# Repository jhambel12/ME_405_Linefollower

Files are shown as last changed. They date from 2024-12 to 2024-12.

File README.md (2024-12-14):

# ME_405_Linefollower

**Cal Poly Mechatronics Line Follower Robot**

This project involves a Romi robot configured and programmed using micropython to autonomously complete a line-following course and return to its initial start point. This involves line detection, bump detection, and relative position tracking. This work was completed by **Jack Ellis** and **Jacob Hambel**, with guidance and support from **Charlie Refvem**. 

---

## Main Features

- **Line Following Capability**: The robot uses infrared sensors to detect and follow a predefined line.
- **Obstacle Detection and Avoidance**: Equipped with bump sensors to handle unexpected obstacles.
- **Position Tracking**: Returns from the start box after completing the course.

---

## Components Used

### Hardware:
- **Romi Chassis and Components**
- **BNO055 IMU sensor**: Detects acceleration, angular rate, and magnetic fields. Note - handle with care as it is sensitive to impact.
- **Infrared Line Sensors**: Five ITR20001/T infrared sensors for line detection.
- **Bump Sensor**: Detects obstacles to avoid collisions.

### Mechanical Design Files:
- `Line Sensor Mount` - [View Line Sensor Mount](./CAD/Lower_Bracket.STL)  
- `Bump Sensor Mount` - [View Bump Sensor Mount](./CAD/Upper_Bracket.STL)  
- `Bump Sensor Bumper` - [Bump Sensor Bumper](./CAD/Bump_Sensor.STL)  
-    Bump sensor bumper is optional, the reason for its use in this project is to reduce the weight offset in the front.

---

## Wiring Information
- **Nucleo Pinout diagrams**
    See the Morpho Headers section on the [ST Nucleo-L475RG webpage](https://os.mbed.com/platforms/ST-Nucleo-L476RG/).  
- **Wiring Diagram**
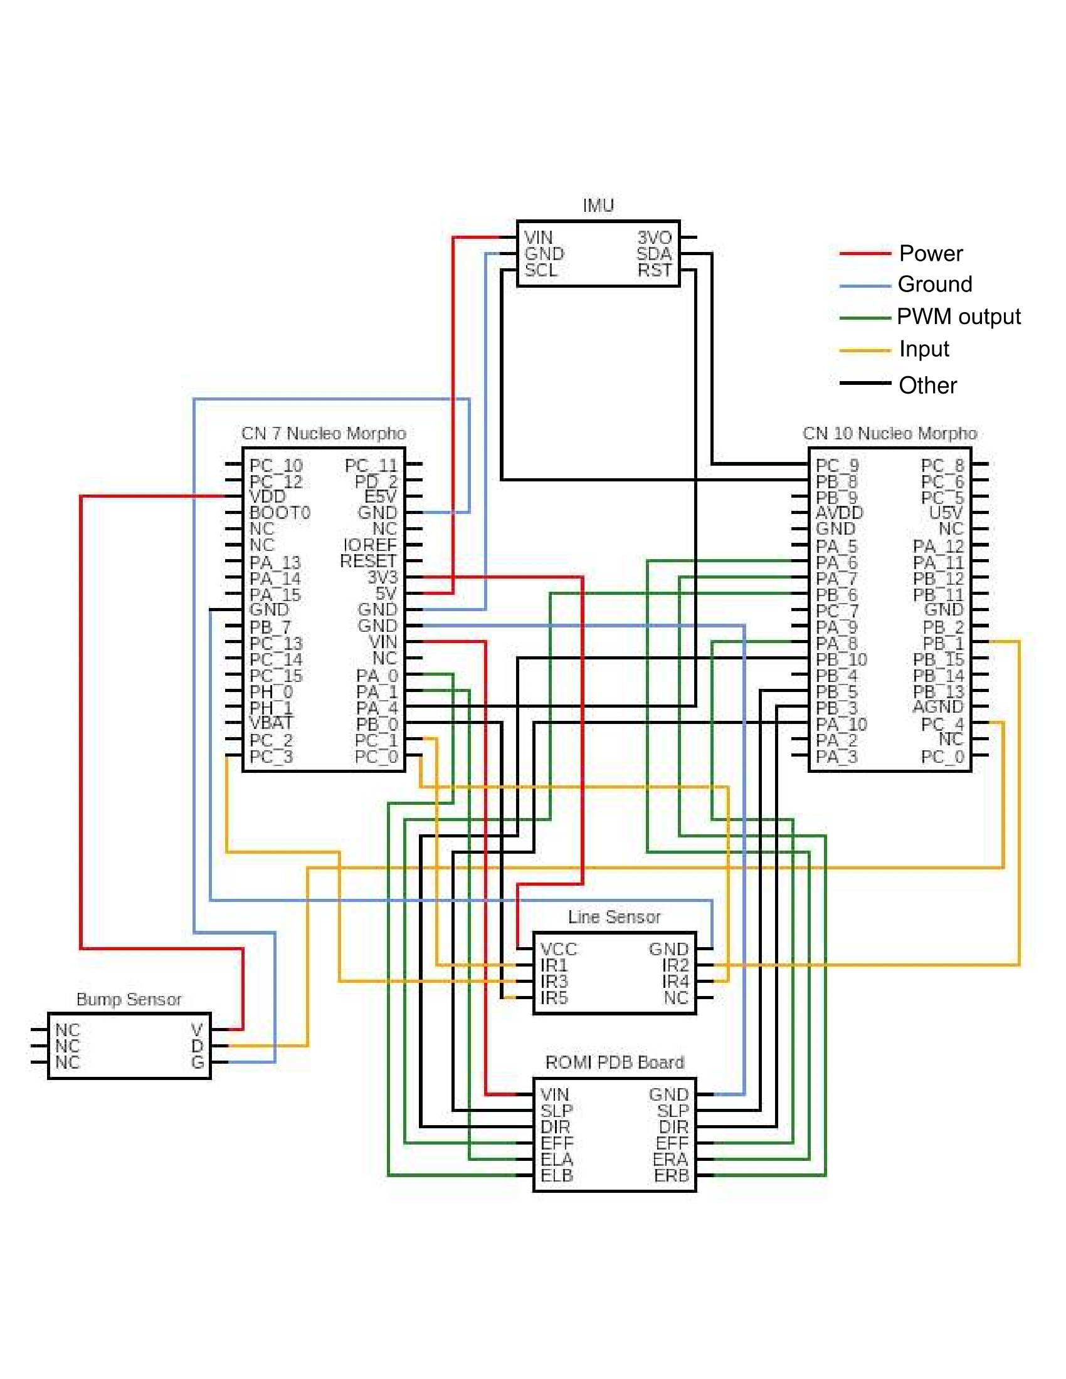
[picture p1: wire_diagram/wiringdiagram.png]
Wiring Diagram
  

- **Pin assignment table**    

| Pin Name Nucleo | Pin Mode | Connection | Pin Name on device |
| --- | --- | --- | --- |
| PB_5 | Output, Push/Pull | Left Motor Enable | Not Sleep text |
| PB_3 | Output, Push/Pull | Left Motor Direction | DIR |
| PA_8 | Timer 1 CH 1 | Left Motor effort | PWM |
| PA_10 | Output, Push/Pull | Right Motor Enable | Not Sleep text | 
| PB_10 | Output, Push/Pull | Right Motor Direction | DIR |
| PB_6 | Timer 4 CH 1 | Right Motor effort | PWM |
| PA_6 | Timer 3 CH 1 | Right Encoder | ERB |
| PA_7 | Timer 3 CH 2 | Right Encoder | ERA |
| PA_0 | Timer 2 Ch 1 | Left Encoder | ELB |
| PA_1 | Timer 2 Ch 2 | Left Encoder | ELA |
| PC_1 | Analog input | Line sensor | IR1 |
| PB_1 | Analog input | Line sensor | IR2 |
| PC_3 | Analog input | Line sensor | IR3 |
| PC_0 | Analog input | Line sensor | IR4 |
| PB_0 | Analog input | Line sensor | IR5 |
| PC_4 | Analog input | Bump sensor | D |
| PA_4 | Output, Push/Pull | Reset Pin for IMU | RST |
| PB_8 | I2C1 SCL | I2C1 clock for I2C bus | SCL |
| PB_9 | I2C1 SDA | I2C1 serial data for I2C bus | SDA |

---

## Software

The control system implements a **PI control loop**, using encoder data and line sensor readings as feedback to maintain line tracking and accurate trajectory. This program uses cooperative multitasking in a finite state machine to ensure all tasks run on time. To accomplish this, the scheduler is used with priority and duration

### Python Files:
- **`main.py`**: Main program orchestrating the robot’s behavior.  
[View main File](./code/main.py)  
- **`motor.py`**: Controls motor operations.  
[View Motor File](./code/motor.py)  
- **`encoder.py`**: Handles data from the encoders.  
[View IMU File](./code/encoder.py)  
- **`BNO055.py`**: Interface for the BNO055 sensor (if used).  
[View Line Sensor File](./code/BNO055.py)  
- **`irsensor.py`**: Reads data from the infrared sensors.  
[View Bump Sensor File](./code/irsensor.py)  
- **`bumpsensor.py`**: Reads data from the bump sensor.  
[View cotask File](./code/bumpsensor.py)  
- **`cotask.py`**: Manages cooperative multitasking.  
[View task_share File](./code/cotask.py)  
- **`task_share.py`**: Facilitates shared data between tasks.  
[View Main File](./code/task_share.py)  

### Code Functionality:
Main holds the task structure and is the file that runs when the robot is in motion. The code operates as a finite state machine, and it has five tasks. The following task diagram shows the tasks and the shared variables between them. 
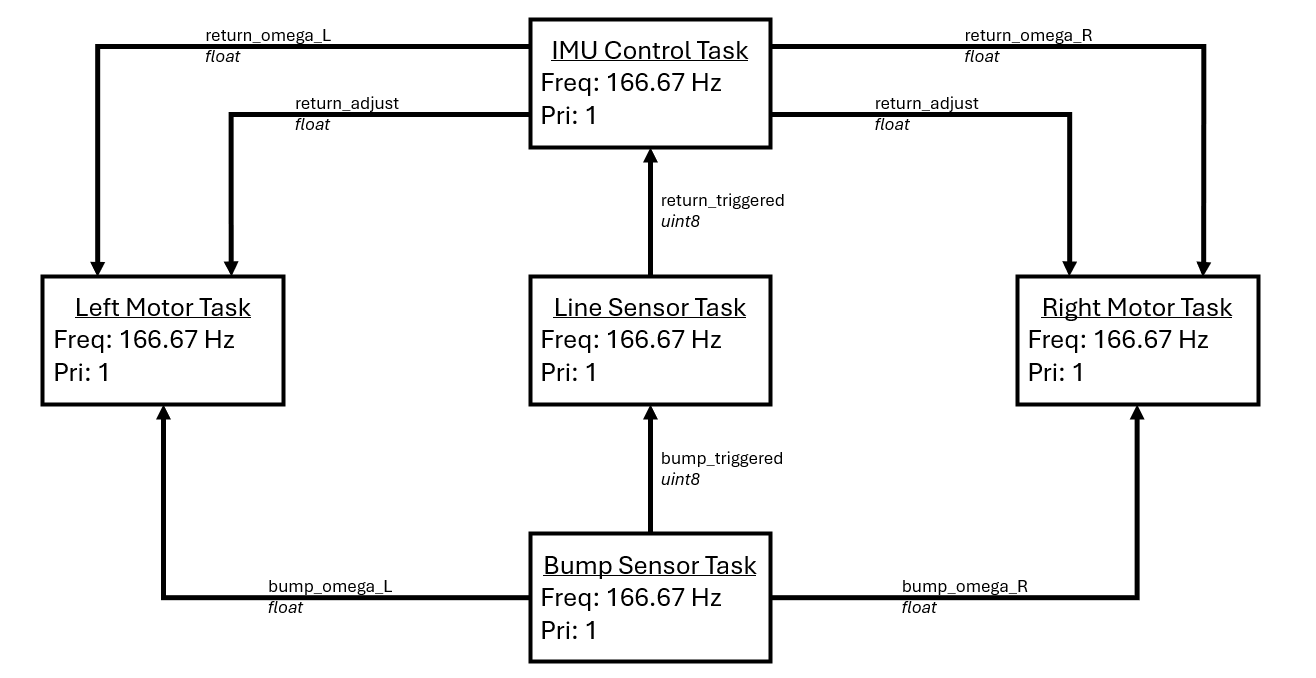
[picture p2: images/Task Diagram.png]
Task Diagram
 

Below, state transition diagrams are provided for each of the tasks.
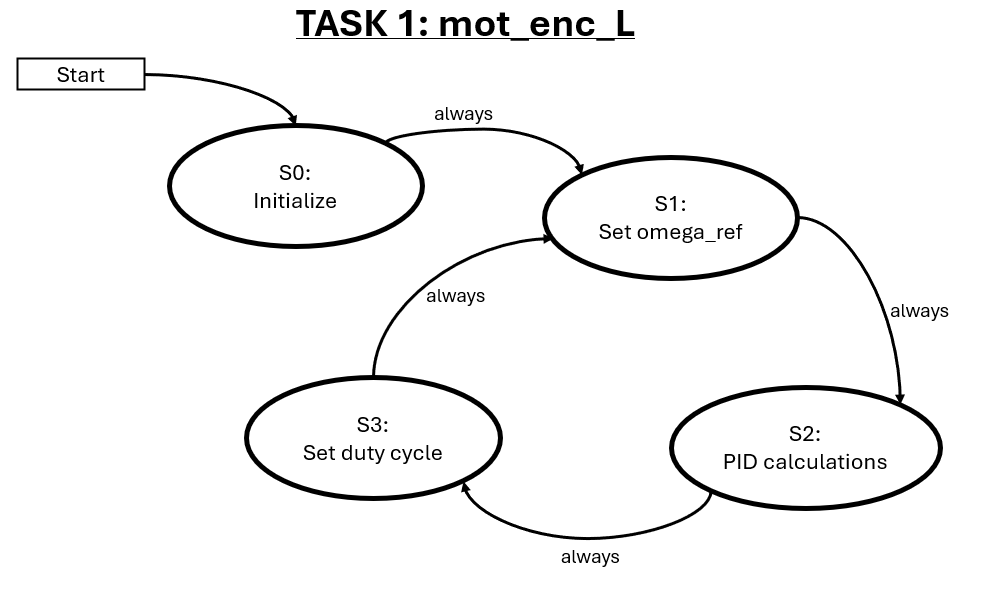
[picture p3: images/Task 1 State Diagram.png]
Task 1
 
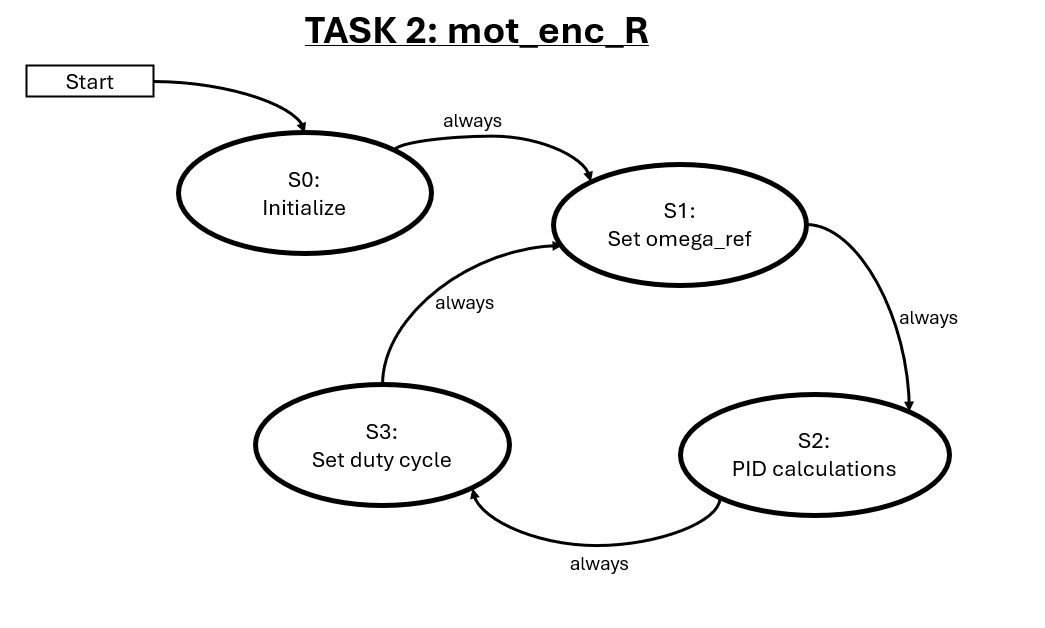
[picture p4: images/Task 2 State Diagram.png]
Task 2
 
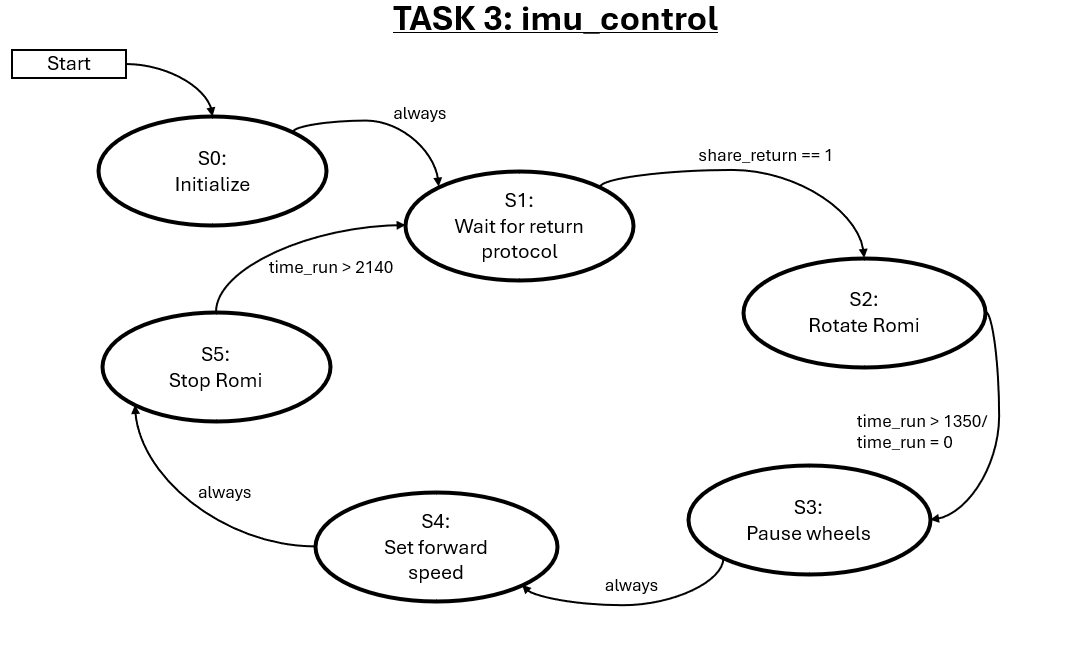
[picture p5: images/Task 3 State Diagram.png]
Task 3
 
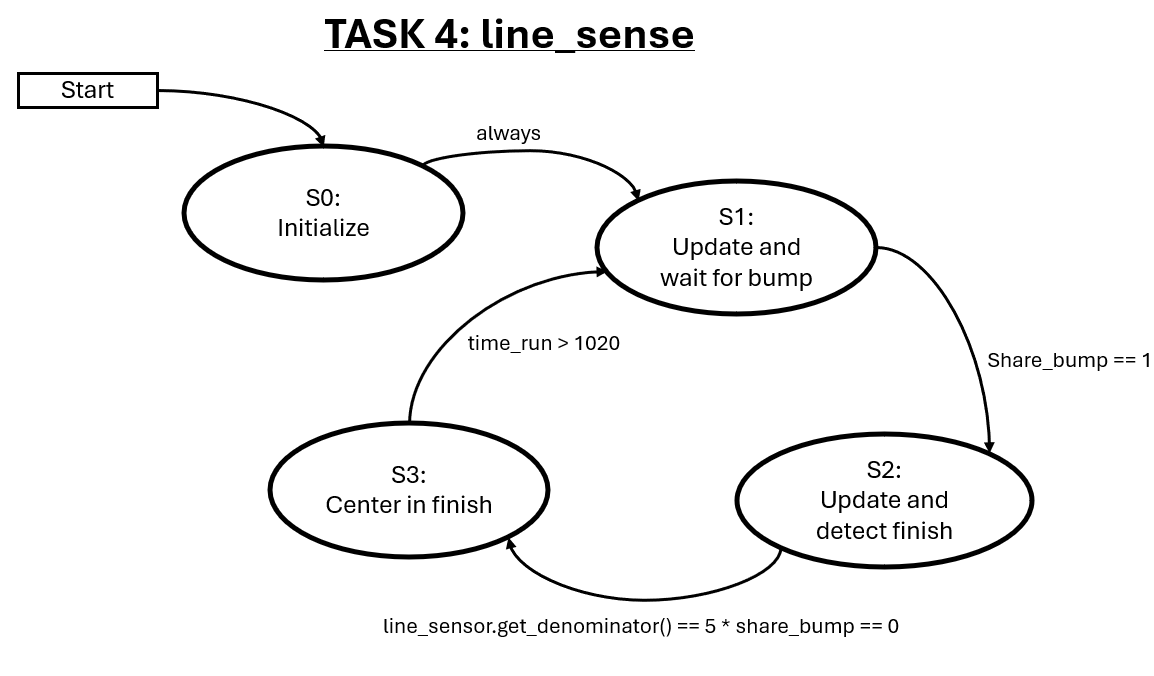
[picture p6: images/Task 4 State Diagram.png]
Task 4
 
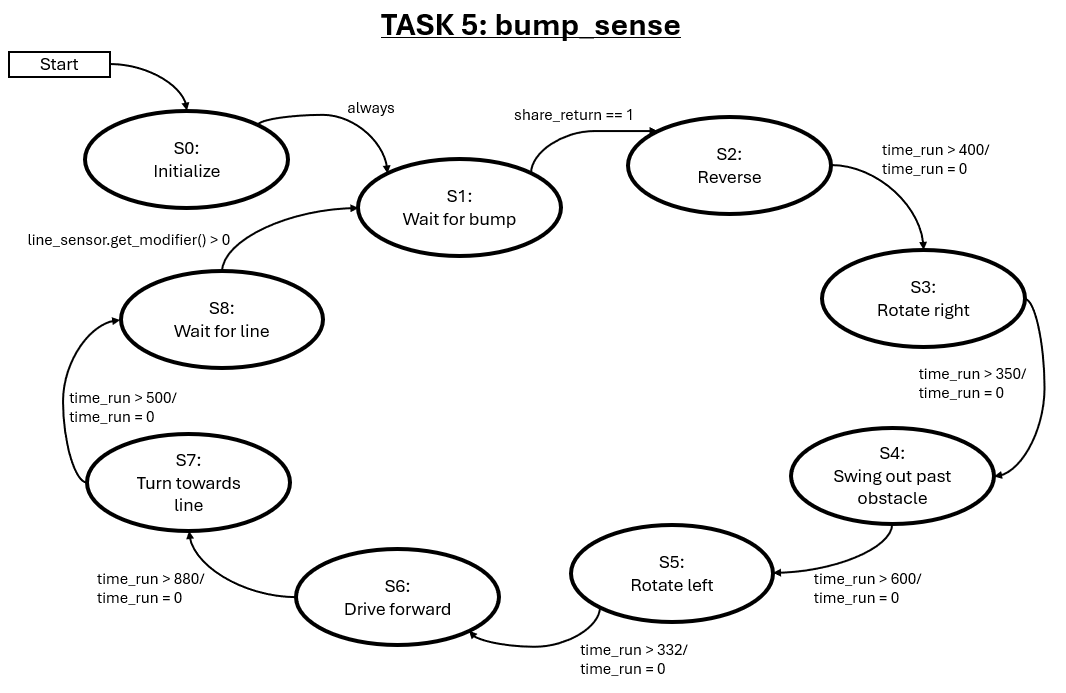
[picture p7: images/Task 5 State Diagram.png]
Task 5
 

Within these tasks, classes are referenced to handle particular functions of the sensors, motor controller, and the IMU that the code interacts with. This keeps the length reasonable and improves the readibility of the code. Overall, the flow of the code wants to stay in line following mode. If the bump sensor is triggered, the obstacle avoidance measures will be taken until it finds a line again. After the bump sensor is triggered, the line sensor mode will look for all 5 sensors to detect a line. When this happens, that means Romi has found the end box. Romi will then proceed to the center of the box and rotate back to its original heading. After a brief pause, the Romi will begin driving straight on the original heading for a specified time until it returns into the start box. Then, it will stop in the start box completing the run of the course. Below, the functionality and usage of the imported files and classes is discussed.

#### Motor
The motor class is responsible for updating the effort, direction, and enabling the motors. This class is called in 2 tasks by main to control each motor. The effort of the motor is output from a PWM at a duty cycle specified by the controller to attempt to create zero steady state error between the encoder readings and the omega reference. 

#### Encoder
The encoder class has several methods, each of which serve as getting data from the encoder. One method, **`update`** updates the encoder position with the current position. The method **`get_delta`** reads the difference between the current and last encoder reading. **`get_position`** returns the current position. These functions, combined with the use of **'utime.ticks()`** allows for calculation of the actual wheel speed. 

#### Line Sensor
The irsensor class is responsible for gathering the analog readings of the 5 infrared sensors, screening them against a threshold value for black or white, and returning them as a true or false. This class compiles the readings of the sensors into a 5 value list. This is convenient because based on which sensor reads the black value of 1, that is where the line is. To use this as feedback, each position is assigned a value, -4,2,0,2,4 reading left to right. Performing a dot product on these lists determines a value, either positive or negative, that becomes a modifier on the wheel speed set points. The class then returns this modifier for use in the control loop.

#### IMU
The BNO055 class is responsible for gathering readings from the IMU. There are many features of this class that are unused. Mainly, data regarding the heading and yaw rate are used in conjunction with wheel speed data from the encoders to track the position relative to start. The data is sent over the I2C bus for the microcontroller and updated each time the class is called.

#### Bump Sensor
The bumpsensor class is used when the robot encounters the wall. The wall is an 8 inch by 8 inch square. The bump sensor becomes an active low when it has been triggered. This is used to transfer out of the line follower mode and into the obstacle avoidance mode.

#### Cotask
This file is provided for this project. Authored by Dr. Ridgely, **`cotask`** contains classes that can run cooperatively scheduled tasks in the context of a multitasking system. It uses the input scheduling algorithm to run tasks on time and in the proper order using closs called **`CoTaskList`**. 

#### Task_share
This file is provided for this project. Authored by Dr. Ridgely, **`task_share`** contains a class to allow tasks to share data without the risk of interrupts corrupting that data. This is very useful as variables may be shared between tasks without the need for global variables.
  
---

## Video
Line follower in action:  
Watch the Video (https://youtu.be/625d_27x-ZY)

---

## Photos
Romi Front View:  
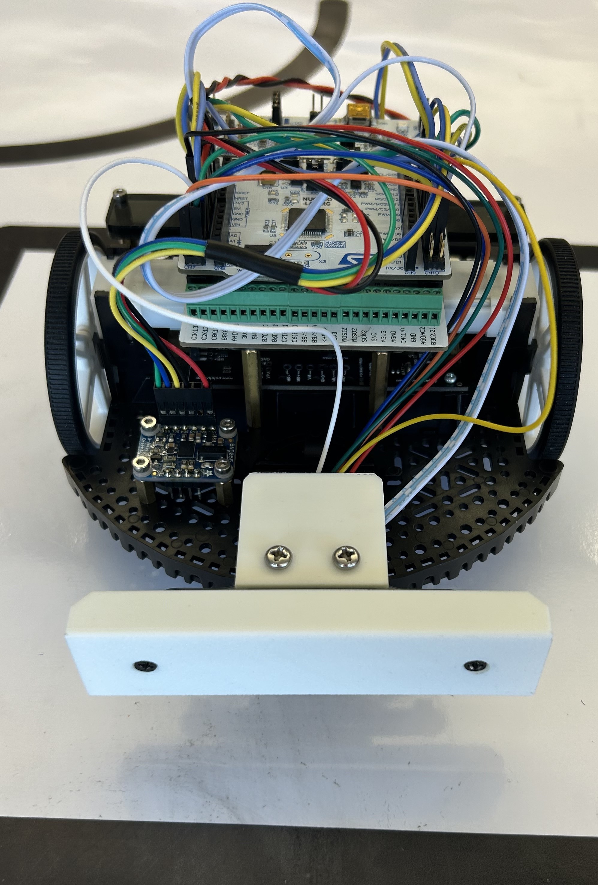
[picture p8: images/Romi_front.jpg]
Robot Front View
  
Romi Top View:  
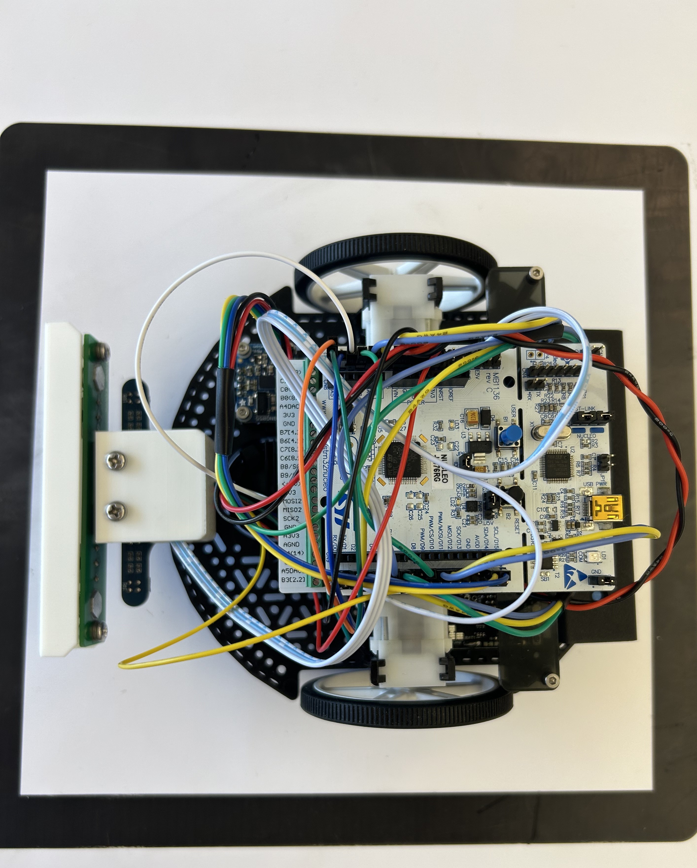
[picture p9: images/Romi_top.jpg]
Robot Top View
  
Romi Side View:  
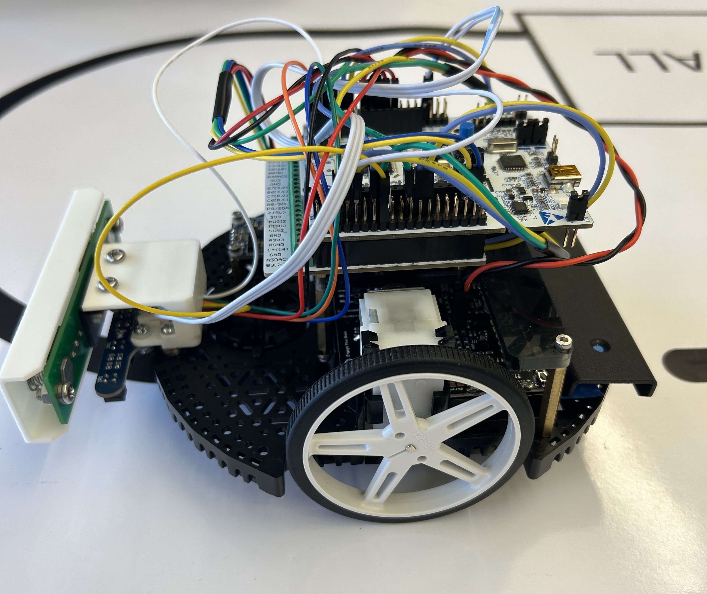
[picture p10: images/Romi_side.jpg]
Robot Side View
  
Romi Isometric View:  
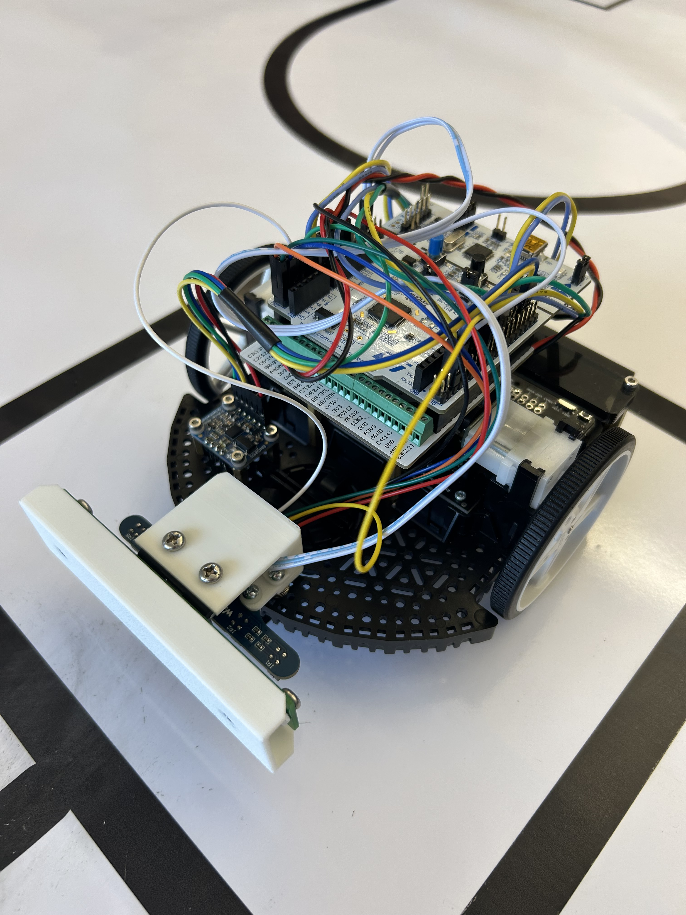
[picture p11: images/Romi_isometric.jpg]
Robot Isometric View
  
Sensor Mounting:  
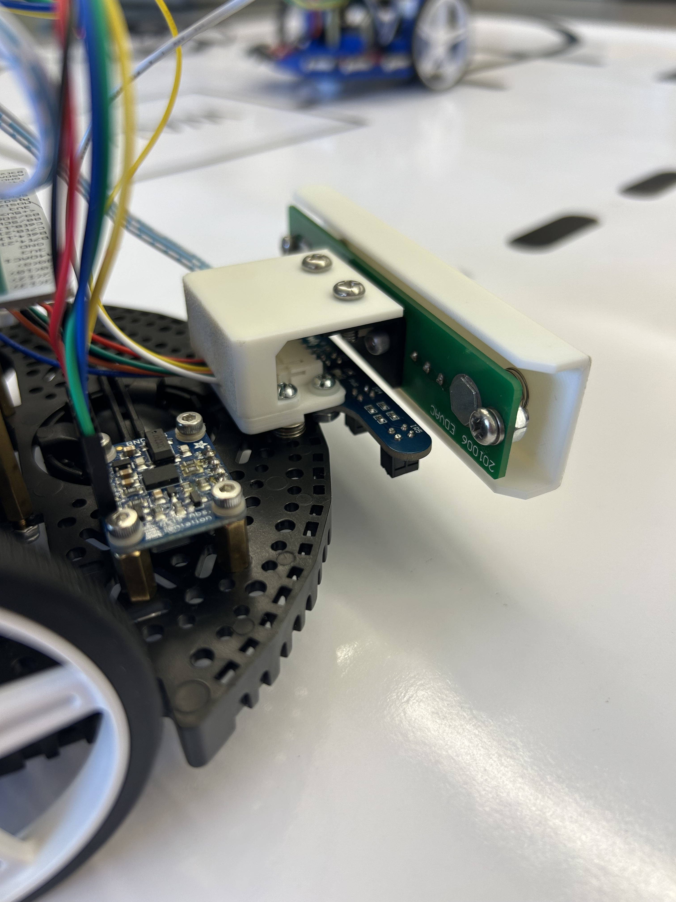
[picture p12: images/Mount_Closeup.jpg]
Sensor Mounting
  
Line Sensor Orientation:  
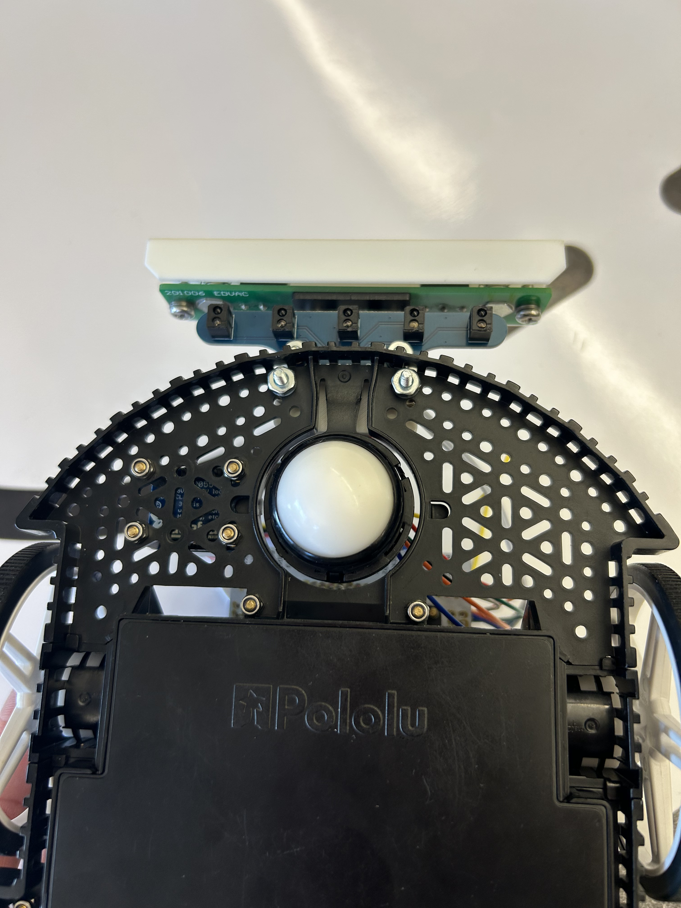
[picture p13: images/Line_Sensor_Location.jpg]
Line Sensor Orientation
  

---

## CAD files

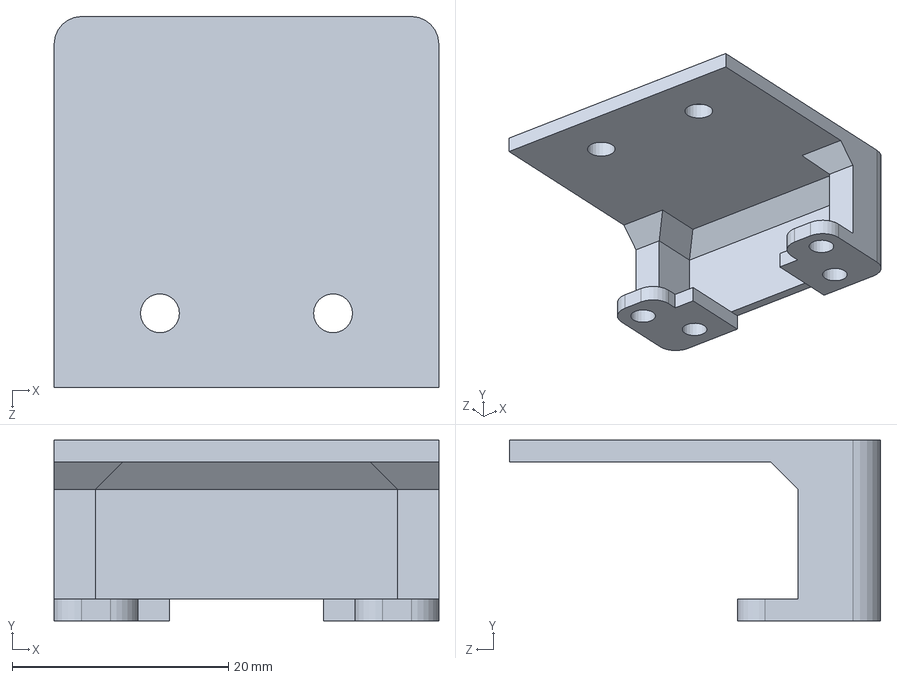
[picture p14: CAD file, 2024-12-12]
CAD/Upper_Bracket.SLDPRT
35.6 x 16.7 x 34.3 mm

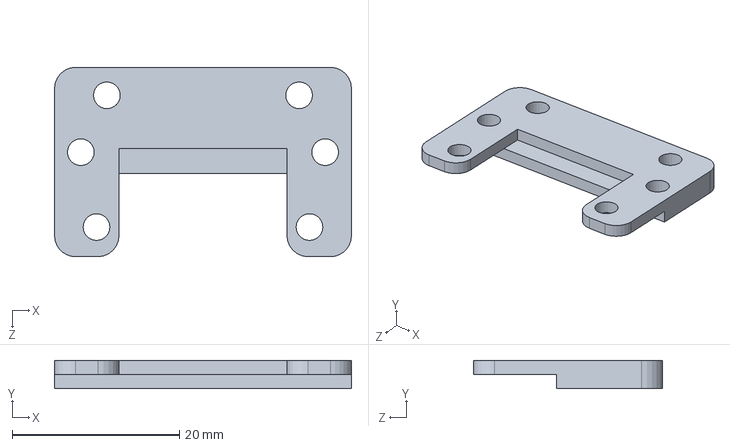
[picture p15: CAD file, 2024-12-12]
CAD/Lower_Bracket.SLDPRT
35.6 x 3.40 x 22.7 mm

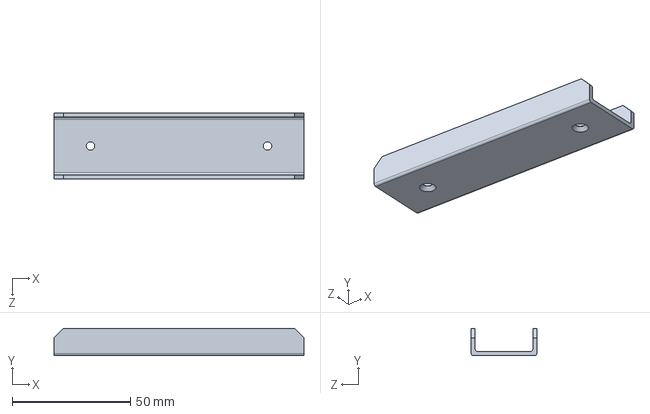
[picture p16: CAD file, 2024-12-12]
CAD/Bump_Sensor.SLDPRT
105.5 x 11.5 x 27.9 mm

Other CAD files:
CAD/Bump_Sensor.STL
CAD/Lower_Bracket.STL
CAD/Upper_Bracket.STL

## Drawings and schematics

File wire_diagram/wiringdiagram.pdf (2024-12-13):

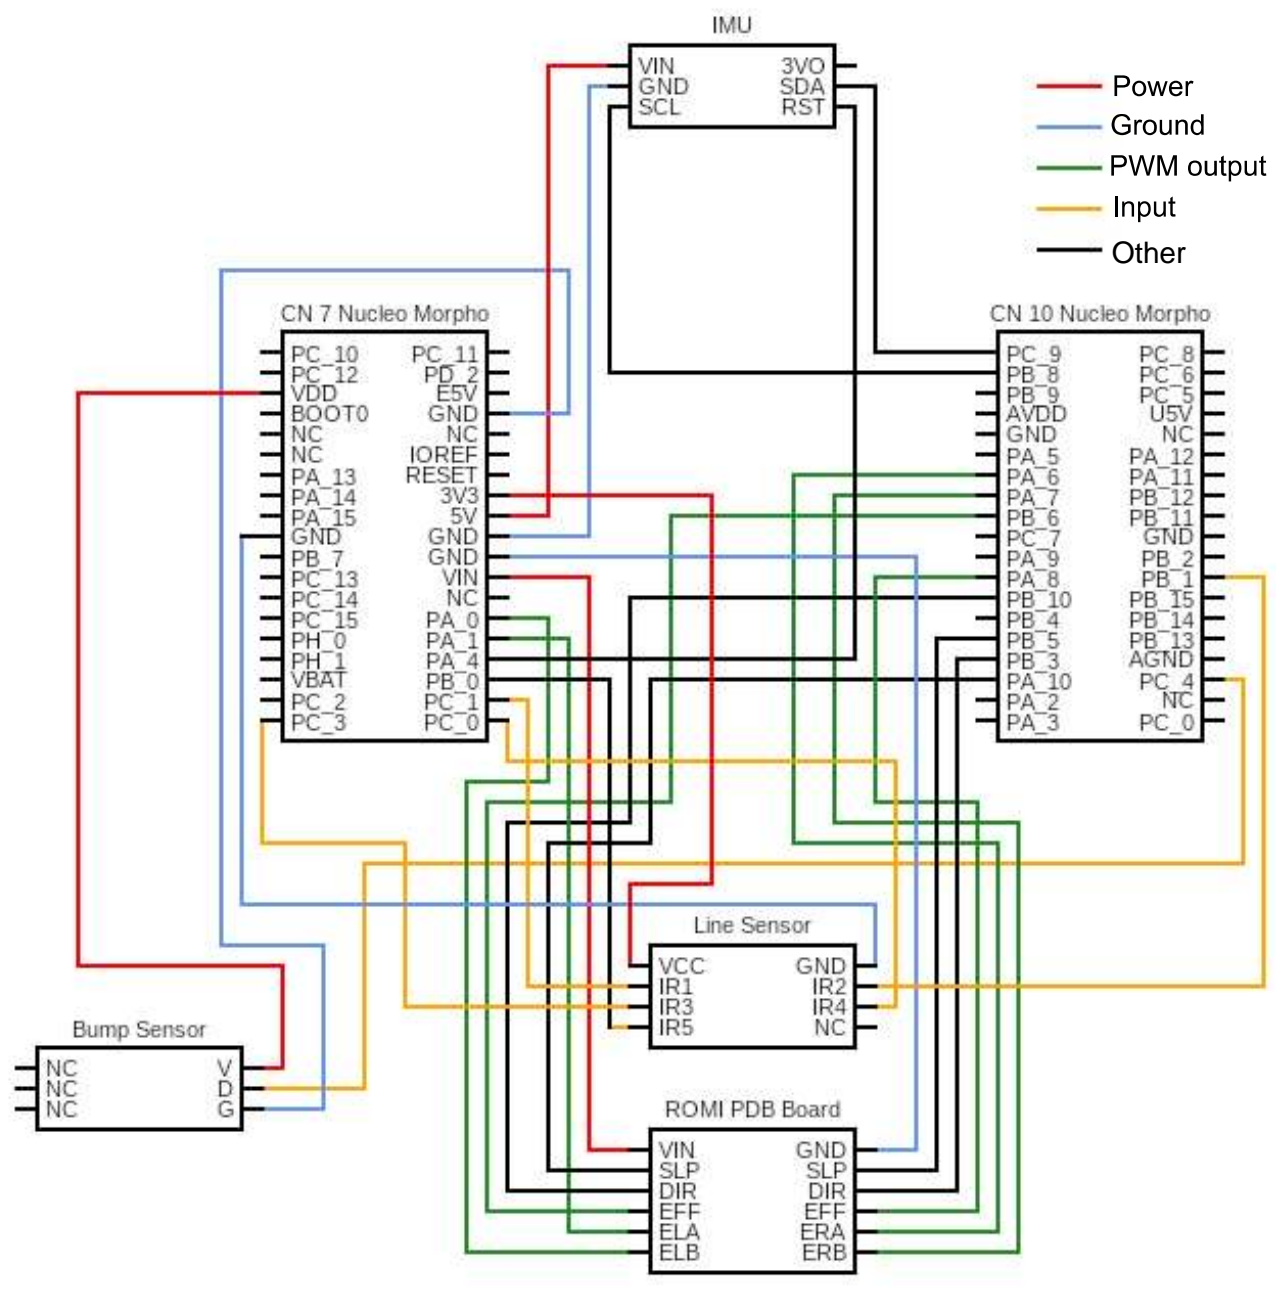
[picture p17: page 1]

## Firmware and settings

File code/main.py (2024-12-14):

'''
@file          main.py
@brief         Main script for autonomous course navigation of a Romi robot
@details       This script implements the control necessary for a Romi differential
               drive robot to navigate a course using line sensors and a bump
               sensor to determine the path for the Romi to take. Each motor 
               operates with a PID control loop using feedback from encoders and an
               IMU as needed.
@author        Jack Ellis, Jacob Hambel
@date          December 13, 2024
'''

#==================================================================================#
# Import necessary modules and classes                                             #
#==================================================================================#

import cotask
import task_share
import gc
import utime

from pyb import Pin, Timer, I2C
from array import array
from math import pi

from encoder import Encoder
from motor import Motor
from BNO055 import BNO055
from irsensor import IRSensor
from bumpsensor import Bumpsensor

#==================================================================================#
# Tasks                                                                            #
#==================================================================================#

# Task 1
def mot_enc_L(shares):
    '''
    @brief    Task 1: Control task for the left motor
    @details  This task intializes the left motor and encoder, performs the PID 
              control calculations, and sets the duty cycle.
    '''

    share_bump , share_omega_L , share_return , share_return_omega_L ,\
    share_heading_adjust = shares

    state = 0
    while True:
        
        # Initialize necessary variables and prepare the motor and encoder
        if state == 0:
            mot_L.enable()          # Enable the left motor
            enc_L.zero()            # Zero the encoder position
            old = utime.ticks_us()  # Store the current time
            mot_L.set_dir(True)     # Set motor direction
            K_p = 130               # Proportional gain constant
            K_i = 2                 # Integral gain constant
            K_d = 60               # Derivative gain constant
            err_old = 0             # Old error value for derivative control
            int_err = 0             # Integral error for integral control
            state = 1      

        # Detect if either the bump protocol or return protocol are active, and use
        # their prescribed velocities if they are. Otherwise, default to the line
        # sensor for control
        elif state == 1:
            if share_bump.get() == 1:
                int_err = 0
                omega_ref = share_omega_L.get()
            elif share_return.get() == 1:
                int_err = 0
                omega_ref = share_return_omega_L.get() + share_heading_adjust.get()
            else:
                adjust = line_sensor.get_modifier()
                omega_ref = (V_romi + ((adjust*V_romi)/4)) / r_wheel
            state = 2

        # Perform the encoder reading of velocity and calculation of errors for the
        # PID loop
        elif state == 2:
            now = utime.ticks_us()
            t_step = utime.ticks_diff(now, old)
            old = now
            enc_L.update()
            omega_meas = enc_L.get_delta() * ((12500 * pi) / 9) // t_step
            err = (omega_ref - omega_meas)
            int_err += err * t_step
            int_err = max(-20, min(int_err, 20))
            dif_err = (err - err_old) // t_step
            err_old = err
            state = 3

        # Calculate and set the duty cycle using the PID function
        elif state == 3:
            duty = (K_p * (omega_ref - abs(omega_meas)) + K_i * int_err
                    + K_d * dif_err)/28
            mot_L.set_duty(duty)
            state = 1

        yield None

#----------------------------------------------------------------------------------#

# Task 2
def mot_enc_R(shares):
    '''
    @brief    Task 2: Control task for the right motor
    @details  This task initializes the right motor and encoder, performs the PID
              control calculations, and sets the duty cycle.
    '''

    share_bump , share_omega_R , share_return , share_return_omega_R ,\
    share_heading_adjust = shares

    state = 0
    while True:
        
        # Initialize necessary variables and prepare the motor and encoder
        if state == 0:
            mot_R.enable()          # Enable the right motor
            enc_R.zero()            # Zero the encoder position
            old = utime.ticks_us()  # Store the current time
            mot_L.set_dir(True)     # Set motor direction
            K_p = 130               # Proportional gain constant
            K_i = 2                 # Integral gain constant
            K_d = 60               # Derivative gain constant
            err_old = 0             # Old error value for derivative control
            int_err = 0             # Integral error for integral control
            state = 1      

        # Detect if either the bump protocol or return protocol are active, and use
        # their prescribed velocities if they are. Otherwise, default to the line
        # sensor for control
        elif state == 1:
            if share_bump.get() == 1:
                int_err = 0
                omega_ref = share_omega_R.get()
            elif share_return.get() == 1:
                int_err = 0
                omega_ref = share_return_omega_R.get() - share_heading_adjust.get()
            else:
                adjust = line_sensor.get_modifier()
                omega_ref = (V_romi - ((adjust*V_romi)/4)) / r_wheel
            state = 2

        # Perform the encoder reading of velocity and calculation of errors for the
        # PID loop
        elif state == 2:
            now = utime.ticks_us()
            t_step = utime.ticks_diff(now, old)
            old = now
            enc_R.update()
            omega_meas = enc_R.get_delta() * ((12500 * pi) / 9) // t_step
            err = (omega_ref - omega_meas)
            int_err += err * t_step
            int_err = max(-20, min(int_err, 20))
            dif_err = (err - err_old) // t_step
            err_old = err
            state = 3

        # Calculate and set the duty cycle using the PID function
        elif state == 3:
            duty = (K_p * (omega_ref - abs(omega_meas)) + K_i * int_err
                    + K_d * dif_err)/23.34
            mot_R.set_duty(duty)
            state = 1

        yield None

#----------------------------------------------------------------------------------#

# Task 3
def imu_control(shares):
    '''
    @brief    Task 3: Control task for the IMU
    @details  This task saves the initial heading of the Romi to be used for the 
              return protocol. Once the return protocol is triggered, the IMU
              heading feedback controls the motors.
    '''

    share_return , share_return_omega_L , share_return_omega_R ,\
    share_heading_adjust = shares

    state = 0
    time_run = 0
    while True:

        # Take initial heading reading
        if state == 0:
            start_heading = imu.euler("head")
            state = 1

        # Detect of the return protocol needs to be executed
        elif state == 1:
            if share_return.get() == 1:
                share_return_omega_L.put(0)
                share_return_omega_R.put(0)
                old = utime.ticks_ms()
                state = 2
        
        # Rotate the Romi to generally face the starting box
        elif state == 2:
            now = utime.ticks_ms()
            time_run += utime.ticks_diff(now, old)
            old = utime.ticks_ms()
            mot_L.set_dir(False)
            return_omega_L.put(8)
            return_omega_R.put(8)
            if time_run > 1350:
                time_run = 0
                state = 3

        # Stop the Romi to ensure a smooth start to the return
        elif state == 3:
            mot_L.set_dir(True)
            return_omega_L.put(0)
            return_omega_R.put(0)
            state = 4

        # Set both wheels to a high speed to return quickly
        elif state == 4:
            return_omega_L.put(23)
            return_omega_R.put(23)
            old = utime.ticks_ms()
            state = 5

        # Use heading feeback to align the Romi and keep it on course to the start
        # box. After reaching the start box, disable the motors
        elif state == 5:
            now = utime.ticks_ms()
            time_run += utime.ticks_diff(now, old)
            old = utime.ticks_ms()
            current_heading = imu.euler("head")
            heading_error = current_heading - start_heading
            if heading_error > pi:
                share_heading_adjust.put(1)
            elif heading_error < pi:
                share_heading_adjust.put(-1)
            else:
                share_heading_adjust.put(0)
            if time_run > 2140:
                mot_L.disable()
                mot_R.disable()
                state = 1

        yield None

#----------------------------------------------------------------------------------#

# Task 4
def line_sense(shares):
    '''
    @brief    Task 4: Control task for the line sensors
    @details  This task updates the line sensor readings to prepare a new adjustment
              value for the motors to maintain orientation along the line. After
              cleairng the obstacle, the line sensor class prepares to detect the 
              trigger for the return protocol once entering the finish box.
    '''

    share_bump , share_return = shares

    state = 0
    time_run = 0
    while True:
        
        if state == 0:
            share_return.put(0)
            line_sensor.update()
            state = 1
        
        # Update the line sensor reading and detect if the obstacle has occured
        elif state  == 1:
            if share_bump.get() == 1:
                state = 2
            line_sensor.update()

        # Update the line sensor reading, and once the obstacle protocol has been
        # executed and the finish box is detected, begin the return protocol
        elif state == 2:
            line_sensor.update()
            if line_sensor.get_denominator() == 5 and share_bump.get() == 0:
                old = utime.ticks_ms()
                state = 3

        # Center in the finish box, and relinquish control to the IMU for the
        # return
        elif state == 3:
            now = utime.ticks_ms()
            time_run += utime.ticks_diff(now, old)
            old = utime.ticks_ms()
            if time_run > 1020:
                share_return.put(1)
                state = 1

        yield None

#----------------------------------------------------------------------------------#

# Task 5
def bump_sense(shares):
    '''
    @brief    Task 5: Control task for the bump sensor
    @details  The bump sensor contrl task monitors the bump sensor for triggering,
              and once triggered, it sends desired motor speeds to the motor 
              classes to navigate around the obstacle. Once clearing the obstacle
              and returning to the line, it reliquishes control to the line
              sensors.
    '''

    share_bump, share_omega_L, share_omega_R = shares

    state = 0
    time_run = 0
    while True:
        
        if state == 0:
            share_bump.put(0)
            state =1

        # Detect when a bump occurs and prepare the system to respond
        elif state == 1:
            if bump_sensor.detect() < 2000:
                share_bump.put(1)
                share_omega_L.put(0)
                share_omega_R.put(0)
                mot_L.set_dir(False)
                mot_R.set_dir(False)
                old = utime.ticks_ms()
                state = 2
        
        # Reverse from the obstacle
        elif state == 2:
            now = utime.ticks_ms()
            time_run += utime.ticks_diff(now, old)
            old = utime.ticks_ms()
            share_omega_L.put(8)
            share_omega_R.put(8)
            if time_run > 400:
                time_run = 0
                state = 3
        
        # Rotate right
        elif state == 3:
            now = utime.ticks_ms()
            time_run += utime.ticks_diff(now, old)
            old = utime.ticks_ms()
            mot_L.set_dir(True)
            share_omega_L.put(12)
            share_omega_R.put(12)
            if time_run > 350:
                time_run = 0
                state = 4

        # Drive forward to avoid the obstacle
        elif state == 4:
            now = utime.ticks_ms()
            time_run += utime.ticks_diff(now, old)
            old = utime.ticks_ms()
            mot_R.set_dir(True)
            share_omega_L.put(18)
            share_omega_R.put(18)
            if time_run > 600:
                time_run = 0
                state = 5

        # Rotate left
        elif state == 5:
            now = utime.ticks_ms()
            time_run += utime.ticks_diff(now, old)
            old = utime.ticks_ms()
            mot_L.set_dir(False)
            share_omega_L.put(12)
            share_omega_R.put(12)
            if time_run > 332:
                time_run = 0
                state = 6

        # Drive forward past the obstacle
        elif state == 6:
            now = utime.ticks_ms()
            time_run += utime.ticks_diff(now, old)
            old = utime.ticks_ms()
            mot_L.set_dir(True)
            share_omega_L.put(16)
            share_omega_R.put(16)
            if time_run > 880:
                time_run = 0
                state = 7

        # Turn back towards the path
        elif state == 7:
            now = utime.ticks_ms()
            time_run += utime.ticks_diff(now, old)
            old = utime.ticks_ms()
            share_omega_L.put(4)
            share_omega_R.put(18)
            if time_run > 500:
                time_run = 0
                state = 8

        # Continue straight until ready to relinquich control to the line sensors
        elif state == 8:
            now = utime.ticks_ms()
            time_run += utime.ticks_diff(now, old)
            old = utime.ticks_ms()
            share_omega_L.put(10)
            share_omega_R.put(10)
            if line_sensor.get_modifier() > 0:
                time_run = 0
                share_bump.put(0)
                state = 1

        yield None

#==================================================================================#
# Hardware Initialization and System Parameters                                    #
#==================================================================================#

# Motor objects
tim_L = Timer(1, freq=20_000)       # Timer for left motor
tim_R = Timer(4, freq=20_000)       # Timer for right motor
mot_L = Motor(tim_L, Pin.cpu.B5, Pin.cpu.B3, Pin.cpu.A8)    # Left motor object
mot_R = Motor(tim_R, Pin.cpu.A10, Pin.cpu.B10, Pin.cpu.B6)  # Right motor object

#----------------------------------------------------------------------------------#

# Encoder objects
enc_L = Encoder(2, 65535, 0, Pin.cpu.A0, Pin.cpu.A1)  # Left encoder object
enc_R = Encoder(3, 65535, 0, Pin.cpu.A6, Pin.cpu.A7)  # Right encoder object

#----------------------------------------------------------------------------------#

# Line sensor object
line_sensor = IRSensor([Pin(Pin.board.PC1), Pin(Pin.board.PB1), Pin(Pin.board.PC3), 
               Pin(Pin.board.PC0), Pin(Pin.board.PB0)])     # Line sensor object

#----------------------------------------------------------------------------------#

# Bump sensor object
bump_sensor = Bumpsensor(Pin(Pin.board.PC4))        # Bump sensor object

#----------------------------------------------------------------------------------#

# IMU setup
res_pin = Pin(Pin.cpu.A4, mode=Pin.OUT_PP)      # Reset pin for IMU
res_pin.low()
utime.sleep_ms(10)
res_pin.high()
utime.sleep_ms(650)
i2c = I2C(1, I2C.CONTROLLER, baudrate=400000)   # I2C bus for IMU
imu = BNO055(i2c)                               # IMU object
utime.sleep_ms(100)
imu.op_mode("NDOF")
utime.sleep_ms(10)

#----------------------------------------------------------------------------------#

# Romi geometry
w_romi = 0.0705         # Romi radius
r_wheel = 0.035         # Radius of wheel
V_romi = .35            # Romi velocity

#==================================================================================#
# Scheduler Setup                                                                  #
#==================================================================================#

# Shared variable setup
#
# Flag to communicate to tasks when the bump sensor has been activated
bump_triggered = task_share.Share('B', thread_protect=False, name="BumpTrigger")
# Programmable speed for the left motor to set the obstacle avoidance response
bump_omega_L = task_share.Share('f', thread_protect=False, name="BumpLeftSpeed")
# Programmable speed for the left motor to set the obstacle avoidance response
bump_omega_R = task_share.Share('f', thread_protect=False, name="BumpRightSpeed")
# Flag to communicate to tasks when the return to start protocal is required
return_triggered = task_share.Share('B', thread_protect=False,
                                     name="ReturnTrigger")
# Programmable speed for the left motor to set the return response
return_omega_L = task_share.Share('f', thread_protect=False,
                                   name="ReturnLeftSpeed")
# Programmable speed for the left motor to set the return response
return_omega_R = task_share.Share('f', thread_protect=False,
                                   name="ReturnRightSpeed")
# Variable to inform the motors if the robot is off course during the return and
# correct for the error
return_adjustment = task_share.Share('f', thread_protect=False,
                                      name="ReturnAdjustment")

# Task setup
task1 = cotask.Task(mot_enc_L, name="Task_1", priority=1, period=6,
                    profile=True, trace=False, shares=(bump_triggered,bump_omega_L,
                                return_triggered,return_omega_L,return_adjustment))
task2 = cotask.Task(mot_enc_R, name="Task_2", priority=1, period=6,
                    profile=True, trace=False, shares=(bump_triggered,bump_omega_R,
                                return_triggered,return_omega_R,return_adjustment))
task3 = cotask.Task(imu_control, name="Task_3", priority=1, period=6,
                    profile=True, trace=False, shares=(return_triggered,
                                return_omega_L,return_omega_R,return_adjustment))
task4 = cotask.Task(line_sense, name="Task_4", priority=1, period=6,
                    profile=True, trace=False, shares=(bump_triggered,
                                return_triggered))
task5 = cotask.Task(bump_sense, name="Task_5", priority=1, period=6,
                    profile=True, trace=False, shares=(bump_triggered,
                                bump_omega_L,bump_omega_R))

# Append tasks to the task list
cotask.task_list.append(task1)
cotask.task_list.append(task2)
cotask.task_list.append(task3)
cotask.task_list.append(task4)
cotask.task_list.append(task5)

#----------------------------------------------------------------------------------#

# Garbage collection and scheduler setup
gc.collect()
while True:
    try:
        cotask.task_list.pri_sched()  # Run the task scheduler
    except KeyboardInterrupt:
        break

# Print task information after termination
print('\n' + str(cotask.task_list))
print(task1.get_trace())
print('')

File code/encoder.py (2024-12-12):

'''
@file          encoder.py
@brief         A driver for reading from Quadrature Encoders
@details       This module contains the class that is used for setup and operations of the encoders.
@author        Jack Ellis, Jacob Hambel
@date          November 21, 2024
'''

import pyb
import utime

class Encoder:
    '''
    @brief       Interface with quadrature encoders
    @details     The functions in this class take inputs to intialize the pins to be used by the encoders, 
                 perform measurements of the rotation of the encoders, and perform calculations needed
                 to find motor speed.
    '''

    def __init__(self, N, AR, PS, ENC_Pin_A, ENC_Pin_B):
        '''
        @brief    Constructs an encoder object
        @details  This function initilizes all necessary parameters for the encoder to function.
                  The necessary parameters are explained below.
        @param    N: The timer number associated with the encoder
        @param    AR: The auto-reload value for the encoder ticks
        @param    PS: Prescaler value for the encoder
        @param    ENC_Pin_A: Channel A pin connection
        @param    ENC_Pin_B: Channel B pin connection
        '''
        self.tim = pyb.Timer(N, period = AR, prescaler = PS)
        self.tim.channel(1, pin = ENC_Pin_A, mode=pyb.Timer.ENC_AB)
        self.tim.channel(2, pin = ENC_Pin_B, mode=pyb.Timer.ENC_AB)
        pass

    def update(self):
        '''
        @brief    Updates encoder position and delta
        @details  This function measures the current position of the motor, determines the distance 
                  it has traveled since the last measaurement, accounts for overflow of the encoder ticks,
                  and loads the old count storage with the most recent measurement.
        '''
        self.new_count = self.tim.counter()
        self.delta = utime.ticks_diff(self.new_count, self.old_count)
        if self.delta > 65536/2:
            self.delta -= 65536
        elif self.delta < -65536/2:
            self.delta += 65536
        self.old_count = self.new_count
        pass

    def get_position(self):
        '''
        @brief    Gets the most recent encoder position
        @details  The function returns the value of self.new_count to the object calling the function.
                  It does not perform any calculations, it is only a return.
        @return   The most recently measured position of the encoder.
        '''
        return self.new_count

    def get_delta(self):
        '''
        @brief    Gets the most recent encoder delta
        @details  The function returns the value of self.delta to the object calling the function.
                  It does not perform any calculations, it is only a return.
        @return   The most recently measured delta of the encoder.
        '''
        return self.delta

    def zero(self):
        '''
        @brief    Resets the encoder position to zero
        @details  This function initializes the encoder position to reference future movement off of.
        '''
        self.old_count = self.tim.counter()
        pass

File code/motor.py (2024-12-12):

'''
@file          motor.py
@brief         Module containing the romi motor class
@details       This module contains the class for the romi motors that will be accessed
               by the main file to create motor objects for use in the data collection.
@author        Jack Ellis, Jacob Hambel
@date          November 21, 2024
'''

from pyb import Pin, Timer

class Motor:
    '''
    @brief       Interface with quadrature encoders
    @details     The functions in this class take inputs to intialize the pins to be used by the motors, 
                 control their speed using PWM, and enable the motors to function in PWM. 
    '''    

    def __init__(self,PWM_tim,EN_pin,DIR_pin,EFF_pin):
        '''
        @brief    Constructs an encoder object
        @details  This function initilizes all necessary parameters for the motor to function.
                  The necessary parameters are explained below.
        @param    PWM_tim: The timer number associated with the motor for PWM
        @param    EN_pin: Enables motor to function
        @param    DIR_pin: Sets motor direction
        @param    EFF_pin: Sets PWM for the motor
        '''
        self.ON = Pin(EN_pin, mode=Pin.OUT_PP)
        self.DIR = Pin(DIR_pin, mode=Pin.OUT_PP)
        self.EFF = PWM_tim.channel(1, mode=Timer.PWM, pin = EFF_pin)
        pass

    def set_duty(self,duty):
        '''
        @brief    Sets PWM duty cycle
        @details  This function takes in a value to be used as the percentage duty cycle,
                  and the duty cycle is set using the pyb function pulse_width_percent()
        @param    duty: The duty cycle for the PWM
        '''
        if duty > 100:
            self.EFF.pulse_width_percent(100)
        elif duty < 0:
            self.EFF.pulse_width_percent(0)
        else:
            self.EFF.pulse_width_percent(duty)
        pass
   
    def set_dir(self,forward):
        '''
        @brief    Enables the motor
        @details  This function is called once to enable the motor's function.
        @param    forward: Boolean to set motor direction
        '''
        if forward == True:
            self.DIR.low()
        elif forward == False:
            self.DIR.high()
        pass

    def enable(self):
        '''
        @brief    Enables the motor
        @details  This function is called once to enable the motor's function.
        '''
        self.ON.high()
        pass

    def disable(self):
        '''
        @brief    DIsables the motor
        @details  This function is called once to disable the motor's function.
        '''
        self.ON.low()
        pass

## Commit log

2024-12-12 Added in the cad files for the mounts
    [Bump_Sensor.SLDPRT, Lower_Bracket.SLDPRT, Upper_Bracket.SLDPRT]
2024-12-12 Updated cad files to STL for easier viewing
    [Bump_Sensor.STL, Lower_Bracket.STL, Upper_Bracket.STL]
2024-12-12 Add a place to put a video of romi on the track
2024-12-13 Add wiring diagram to the Readme
2024-12-13 Updated file type for wiring diagram
2024-12-13 Adjusted wiring diagram
2024-12-13 Updated wiring diagram
